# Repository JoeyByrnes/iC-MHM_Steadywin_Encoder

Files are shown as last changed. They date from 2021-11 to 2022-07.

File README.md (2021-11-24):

# iC-MHM_Steadywin_Encoder
PCB Design Files for iC-MHM Based Encoder PCB for the Steadywin v3 Motor

<p align="center">
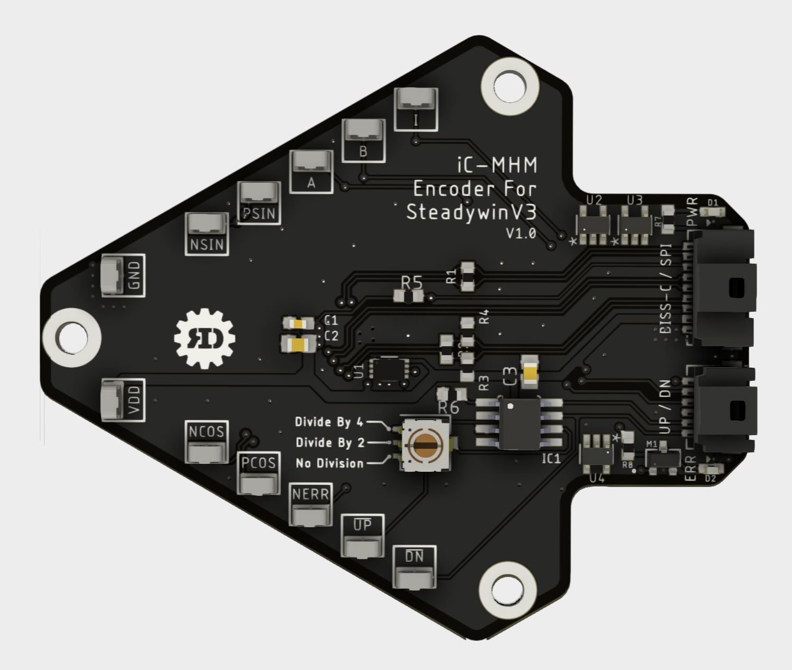
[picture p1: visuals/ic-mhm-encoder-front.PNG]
  
</p>
<p align="center">
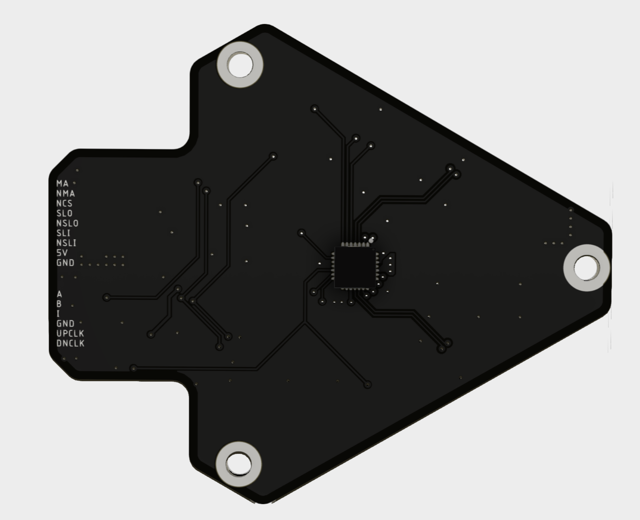
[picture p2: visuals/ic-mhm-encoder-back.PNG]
  
</p>
<p align="center">
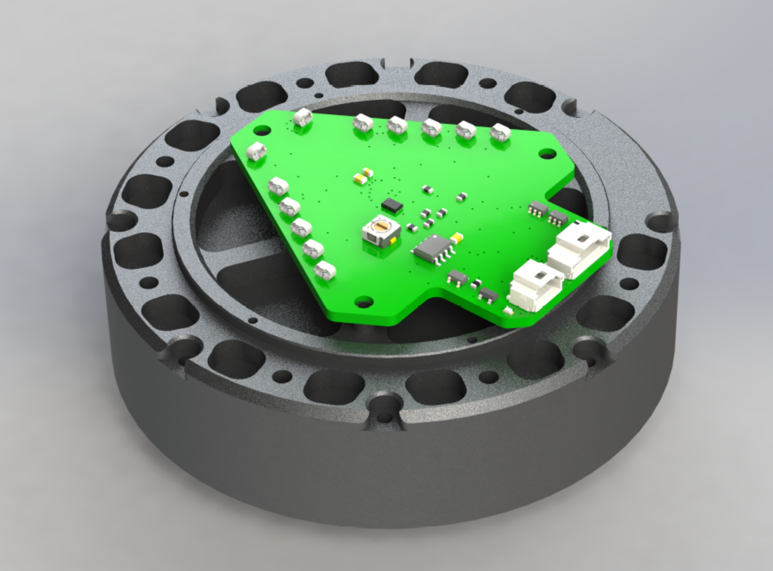
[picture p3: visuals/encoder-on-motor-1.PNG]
  
</p>

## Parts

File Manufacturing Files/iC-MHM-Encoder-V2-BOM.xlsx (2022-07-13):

Manufacturer Part Number | Manufacturer Name | Description | QTY | Digi-Key Part Number 1 | Datasheet | Reference Designator
24LC16BT-I/MC | Microchip Technology | IC EEPROM 16KBIT I2C 400KHZ 8DFN | 1 | 24LC16BT-I/MCCT-ND | https://ww1.microchip.com/downloads/en/DeviceDoc/20001703M.pdf | U1
BSS670S2LH6327XTSA1 | Infineon Technologies | MOSFET N-CH 55V 540MA SOT23-3 | 1 | BSS670S2LH6327XTSA1CT-ND | https://www.infineon.com/dgdl/BSS670S2L_Rev2.5.pdf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 | M1
D5V0F4U6S-7 | Diodes Incorporated | TVS DIODE 5.5VWM 12VC SOT363 | 4 | 31-D5V0F4U6S-7CT-ND | https://www.diodes.com/assets/Datasheets/D5V0F4U6S.pdf | U2, U3, U4, U5
06035C104K4T4A | KYOCERA AVX | CAP CER 0.1UF 50V X7R 0603 | 2 | 478-9903-1-ND | https://datasheets.kyocera-avx.com/AutoMLCC.pdf | C1, C3
0603ZD106KAT2A | KYOCERA AVX | CAP CER 10UF 10V X5R 0603 | 2 | 478-10766-1-ND | https://datasheets.kyocera-avx.com/cx5r.pdf | C2, C4
ERJ-PA3F1200V | Panasonic Electronic Components | RES SMD 120 OHM 1% 1/3W 0603 | 2 | P120BYCT-ND | https://industrial.panasonic.com/cdbs/www-data/pdf/RDO0000/AOA0000C331.pdf | R1, R2
RE0603FRE071KL | YAGEO | RES SMD 1K OHM 1% 1/10W 0603 | 2 | 13-RE0603FRE071KLCT-ND | https://www.yageo.com/upload/media/product/productsearch/datasheet/rchip/PYu-RE_105_RoHS_L_6.pdf | R7, R8
ESR03EZPF1002 | Rohm Semiconductor | RES SMD 10K OHM 1% 1/4W 0603 | 1 | RHM10KADCT-ND | https://fscdn.rohm.com/en/products/databook/datasheet/passive/resistor/chip_resistor/esr-e.pdf | R5
RC0603FR-07845RL | YAGEO | RES 845 OHM 1% 1/10W 0603 | 2 | 311-845HRCT-ND | https://www.yageo.com/upload/media/product/productsearch/datasheet/rchip/PYu-RC_Group_51_RoHS_L_11.pdf | R3, R4
150060RS75000 | Würth Elektronik | LED RED CLEAR 0603 SMD | 1 | 732-4978-1-ND | https://www.we-online.com/katalog/datasheet/150060RS75000.pdf | D2
150060VS75000 | Würth Elektronik | LED GREEN CLEAR 0603 SMD | 1 | 732-4980-1-ND | https://www.we-online.com/katalog/datasheet/150060VS75000.pdf | D1
UA9638CDR | Texas Instruments | IC DRIVER 2/0 8SOIC | 1 | 296-15058-1-ND | https://www.ti.com/general/docs/suppproductinfo.tsp?distId=10 | U6
2023960207 | Molex | CONN HEADER SMD R/A 2POS 1MM | 1 | WM26783CT-ND | https://www.molex.com/pdm_docs/sd/2023960207_sd.pdf | J1
2023961007 | Molex | CONN HEADER SMD R/A 10POS 1MM | 1 | WM26787CT-ND | https://www.molex.com/pdm_docs/sd/2023961007_sd.pdf | J2
iC-MHM | iC-Haus | https://www.ichaus.de/product/ic-mhm | 1 | N/A | https://www.ichaus.de/MHM_datasheet_en | U7

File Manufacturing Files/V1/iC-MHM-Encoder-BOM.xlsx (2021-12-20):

PCB: | Manufacturer Part Number | Manufacturer Name | Description (or link if not on digikey) | Quantity | Digi-Key Part Number 1 | Unit Price | Extended Price | Reference Designator | Datasheet
*** | 2023960607 | Molex | CONN HEADER SMD R/A 6POS 1MM | 1 | 900-2023960607CT-ND | $1.35 | $1.35 | J2 | https://www.molex.com/pdm_docs/sd/2023960607_sd.pdf
 | 2023960907 | Molex | CONN HEADER SMD R/A 9POS 1MM | 1 | WM26786CT-ND | $1.54 | $1.54 | J1 | https://www.molex.com/pdm_docs/sd/2023960907_sd.pdf
 | 24LC16BT-I/MC | Microchip Technology | IC EEPROM 16KBIT I2C 400KHZ 8DFN | 1 | 24LC16BT-I/MCCT-ND | $0.45 | $0.45 | U1 | https://ww1.microchip.com/downloads/en/DeviceDoc/20001703M.pdf
 | BSS670S2LH6327XTSA1 | Infineon Technologies | MOSFET N-CH 55V 540MA SOT23-3 | 1 | BSS670S2LH6327XTSA1CT-ND | $0.45 | $0.45 | M1 | https://www.infineon.com/dgdl/BSS670S2L_Rev2.5.pdf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
 | CS-4-13NTA | Nidec Copal Electronics | SWITCH ROTARY DIP SP3T 100MA 16V | 1 | 563-1035-1-ND | $1.81 | $1.81 | SW1 | https://www.nidec-copal-electronics.com/e/catalog/switch/cs-4.pdf
 | D5V0F4U6S-7 | Diodes Incorporated | TVS DIODE 5.5VWM 12VC SOT363 | 3 | 31-D5V0F4U6S-7CT-ND | $0.52 | $1.56 | U2, U3, U4 | https://www.diodes.com/assets/Datasheets/D5V0F4U6S.pdf
 | LS7183N-S | LSI/CSI | QUADRATURE CLOCK CONVERTER | 1 | 2808-LS7183N-S-ND | $4.89 | $4.89 | IC1 | https://lsicsi.com/datasheets/LS7183N_LS7184N.pdf
 | S1751-46 | Harwin Inc. | PC TEST POINT NATURAL | 12 | 952-3024-ND | $0.23 | $2.78 | U$2, U$3, U$4, U$5, U$6, U$7, U$8, U$9, U$10, U$11, U$15, U$16 | https://cdn.harwin.com/pdfs/S1751.pdf
 | 06035C104K4T4A | KYOCERA AVX | CAP CER 0.1UF 50V X7R 0603 | 2 | 478-9903-1-ND | $0.10 | $0.10 | C1, C4 | https://datasheets.kyocera-avx.com/AutoMLCC.pdf
 | CC0805MRX5R6BB106 | YAGEO | CAP CER 10UF 10V X5R 0805 | 2 | 311-3437-1-ND | $0.20 | $0.40 | C2, C3 | https://www.yageo.com/upload/media/product/productsearch/datasheet/mlcc/UPY-GPHC_X5R_4V-to-50V_26.pdf
 | ERJ-PA3F1200V | Panasonic Electronic Components | RES SMD 120 OHM 1% 1/4W 0603 | 2 | P120BYCT-ND | $0.15 | $0.30 | R1, R2 | https://industrial.panasonic.com/cdbs/www-data/pdf/RDO0000/AOA0000C331.pdf
 | RE0603FRE071KL | YAGEO | RES SMD 1K OHM 1% 1/10W 0603 | 5 | 13-RE0603FRE071KLCT-ND | $0.10 | $0.50 | R7, R8, R9, R10, R11 | https://www.yageo.com/upload/media/product/productsearch/datasheet/rchip/PYu-RE_105_RoHS_L_6.pdf
 | ESR03EZPF1002 | Rohm Semiconductor | RES SMD 10K OHM 1% 1/4W 0603 | 1 | RHM10KADCT-ND | $0.13 | $0.13 | R5 | https://fscdn.rohm.com/en/products/databook/datasheet/passive/resistor/chip_resistor/esr-e.pdf
 | ERJ-3EKF6493V | Panasonic Electronic Components | RES SMD 649K OHM 1% 1/10W 0603 | 1 | P649KHCT-ND | $0.10 | $0.10 | R6 | https://industrial.panasonic.com/cdbs/www-data/pdf/RDA0000/AOA0000C304.pdf
 | RC0603FR-07845RL | YAGEO | RES 845 OHM 1% 1/10W 0603 | 2 | 311-845HRCT-ND | $0.10 | $0.20 | R3, R4 | https://www.yageo.com/upload/media/product/productsearch/datasheet/rchip/PYu-RC_Group_51_RoHS_L_11.pdf
 | 150060RS75000 | Würth Elektronik | LED RED CLEAR 0603 SMD | 1 | 732-4978-1-ND | $0.15 | $0.15 | D2 | https://www.we-online.de/katalog/datasheet/150060RS75000.pdf
 | 150060VS75000 | Würth Elektronik | LED GREEN CLEAR 0603 SMD | 1 | 732-4980-1-ND | $0.15 | $0.15 | D1 | https://www.we-online.de/katalog/datasheet/150060VS75000.pdf
 | iC-MHM | iC Haus | https://www.ichaus.de/product/ic-mhm | 1 | N/A |  |  | U$1 | https://www.ichaus.de/MHM_datasheet_en
 | SN74LVC3G07QDCURQ1 | Texas Instruments | IC BUFFER NON-INVERT 5.5V 8VSSOP | 1 | 296-23710-1-ND | $0.68 | $0.68 | U5 | https://www.ti.com/general/docs/suppproductinfo.tsp?distId=10
*** | The 2023960607 is out of stock on digikey but is available on mouser: |  | https://www.mouser.com/ProductDetail/Molex/202396-0607?qs=5aG0NVq1C4ymp4Cu3BzYEA%3D%3D
Cables: |  |  |  |  |  |  |  | Notes:
 | 5011893010 | Molex | CONN RECEPT 1MM DUAL 30POS | 1 | 23-5011893010-ND | 0.68000 | $0.68 | AMC side absolute connector
 | 5013300600 | Molex | CONN RCPT 1MM VERT 6POS | 1 | WM7919-ND | 0.34000 | $0.34 | iC-MHM side incremental connector
 | 5013300900 | Molex | CONN RCPT 1MM VERT 9POS | 1 | 23-5013300900-ND | 0.41000 | $0.41 | iC-MHM side absolute connector
 | 5013340000 | Molex | CONN SOCKET 28-32AWG CRIMP TIN | 25 | WM3670CT-ND | 0.04300 | $1.08 | Crimps to make custom length cables
 | 0797581018 | Molex | PICO-CLASP 150MM 28AWG PRE-CRIMP | 20 | WM15696-ND | 1.00200 | $20.04 | One option for pre-crimped cables, only 150mm long
 |  |  |  |  |  |  |  | I order all earthsense cables from this supplier, I can check how much the cables we need would cost if we know the length needed, they're very affordable and always provide reliable cables. It usually takes about 3-4 weeks in total to receive orders
 |  |  |  |  |  |  |  | https://ykt.en.alibaba.com/?spm=a2700.12243863.0.0.38403e5f2DNDKv

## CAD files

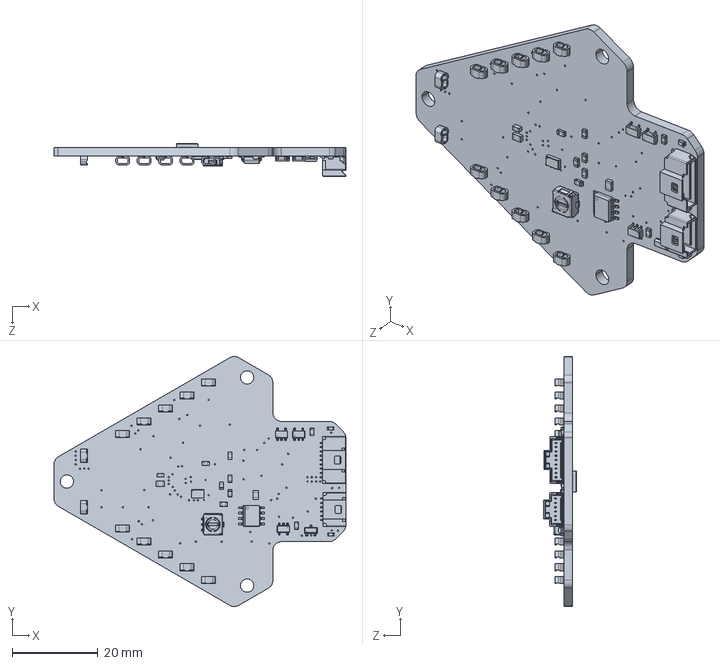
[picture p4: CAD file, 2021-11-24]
3D CAD/ic-mhm-encoder.SLDPRT
68.0 x 58.3 x 7.59 mm

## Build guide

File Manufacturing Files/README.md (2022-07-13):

# How to Order the iC-MHM Encoder:

#### The PCBs are designed to PCBWay's 4-Layer stackup, any thickness from 0.6mm to 2.4mm. 
#### If ordered elsewhere, please confirm that the layer thicknesses are correct before ordering to acheive the correct differential impedances
<hr>

## For an assembly order, enter the following:
15 Unique Components <br>
23 SMD Components total <br>
0 Thru-Hole components <br>
<p>
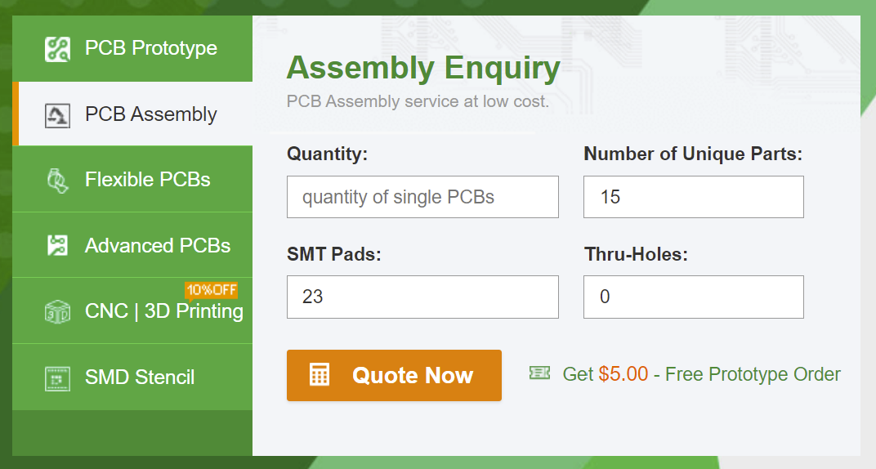
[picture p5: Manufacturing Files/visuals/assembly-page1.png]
  
</p>

### See readme in V1 folder for PCB options, but remember the following changes:
#### The size of the PCB is now 63mm x 58mm (not 68x58)
#### The thickness can be anything from 0.6mm to 2.4mm now
#### the stencil doesnt apply for an assembly order
#### Make sure to upload both the BOM and the zip file which contains the gerbers and the PnP files

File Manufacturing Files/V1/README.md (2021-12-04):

# How to Order the iC-MHM Encoder:

<b>
The PCBs are designed to PCBWay's 4-Layer 2mm stackup. If ordered elsewhere, please confirm that the layer thicknesses are correct before ordering to acheive the correct differential impedances.
</b>
<h2>On the first page of PCBway, enter the following:
<p align="center">
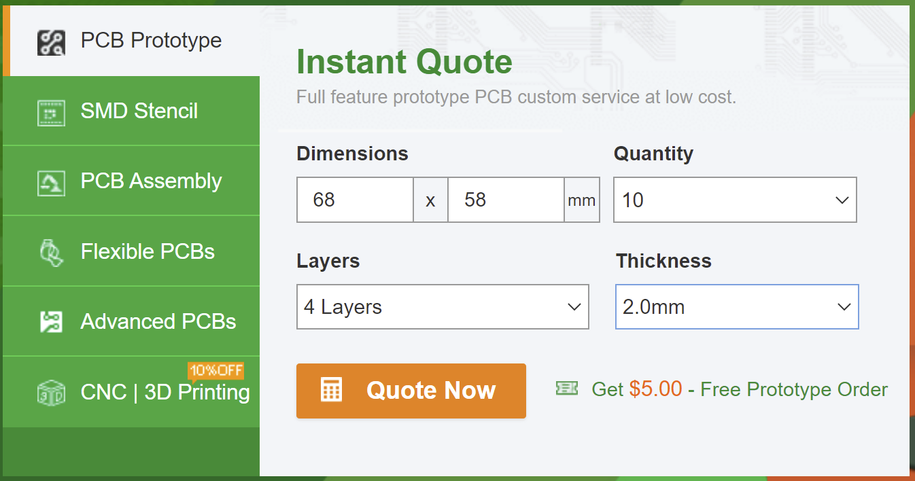
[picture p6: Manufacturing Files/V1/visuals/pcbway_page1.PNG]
  
</p>

On the ordering page, make sure to select 2mm, and choose the color black if you don't want a lame green pcb
<p align="center">
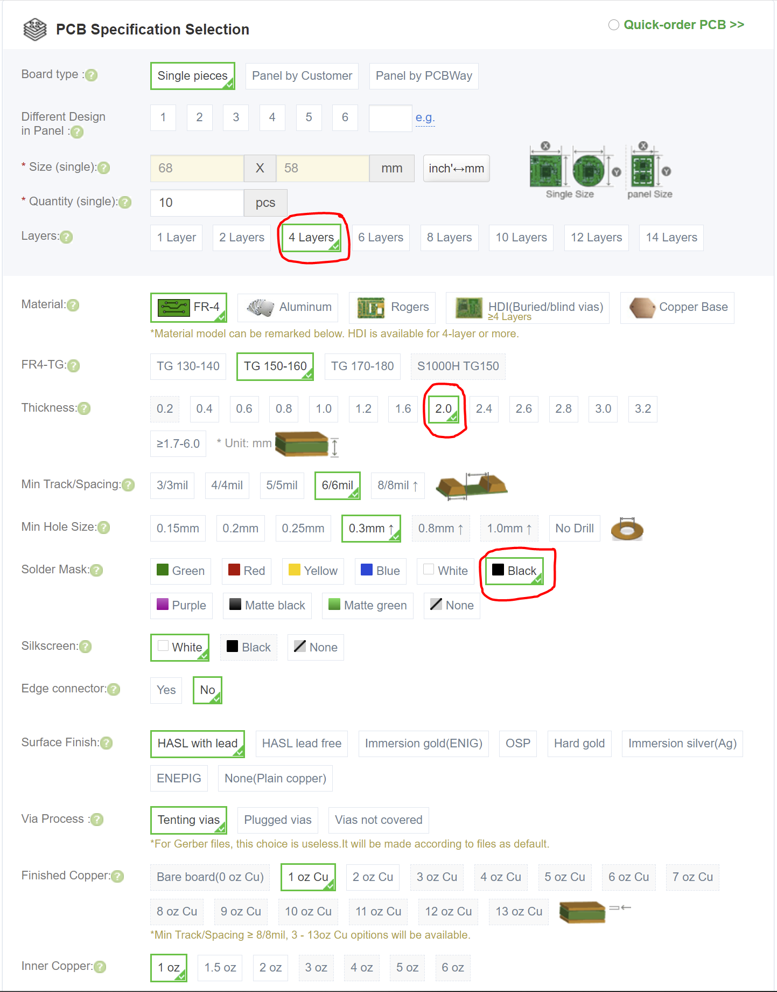
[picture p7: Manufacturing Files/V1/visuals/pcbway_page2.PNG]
  
</p>

Make sure to order a stencil, and that you select Top+Bottom. I find that without framework is easier to use.
<p align="center">
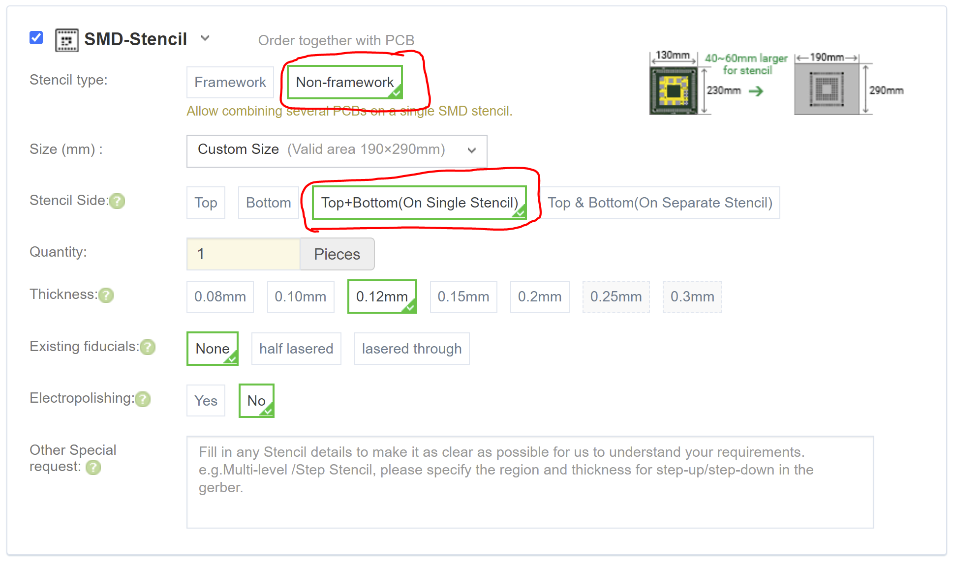
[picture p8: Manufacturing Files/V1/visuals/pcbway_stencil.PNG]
  
</p>

This should be the approximate cost if entered correctly, based on data from 12/4/21
<p align="center">
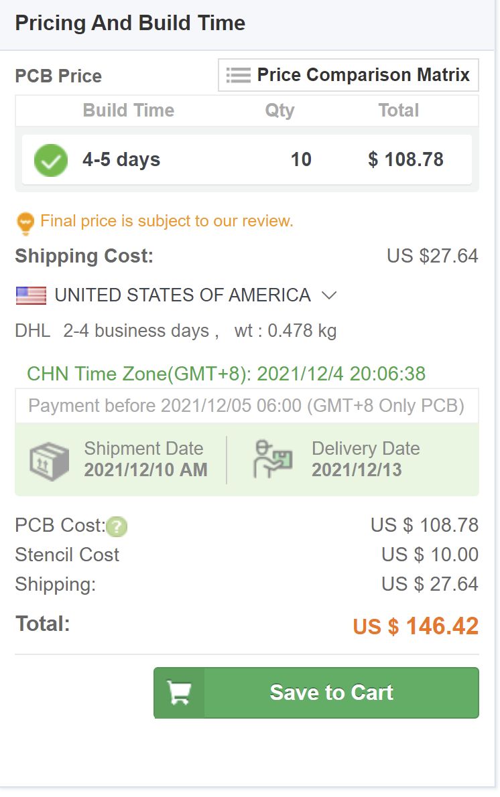
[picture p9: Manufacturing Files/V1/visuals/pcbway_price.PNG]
  </h2>
</p>

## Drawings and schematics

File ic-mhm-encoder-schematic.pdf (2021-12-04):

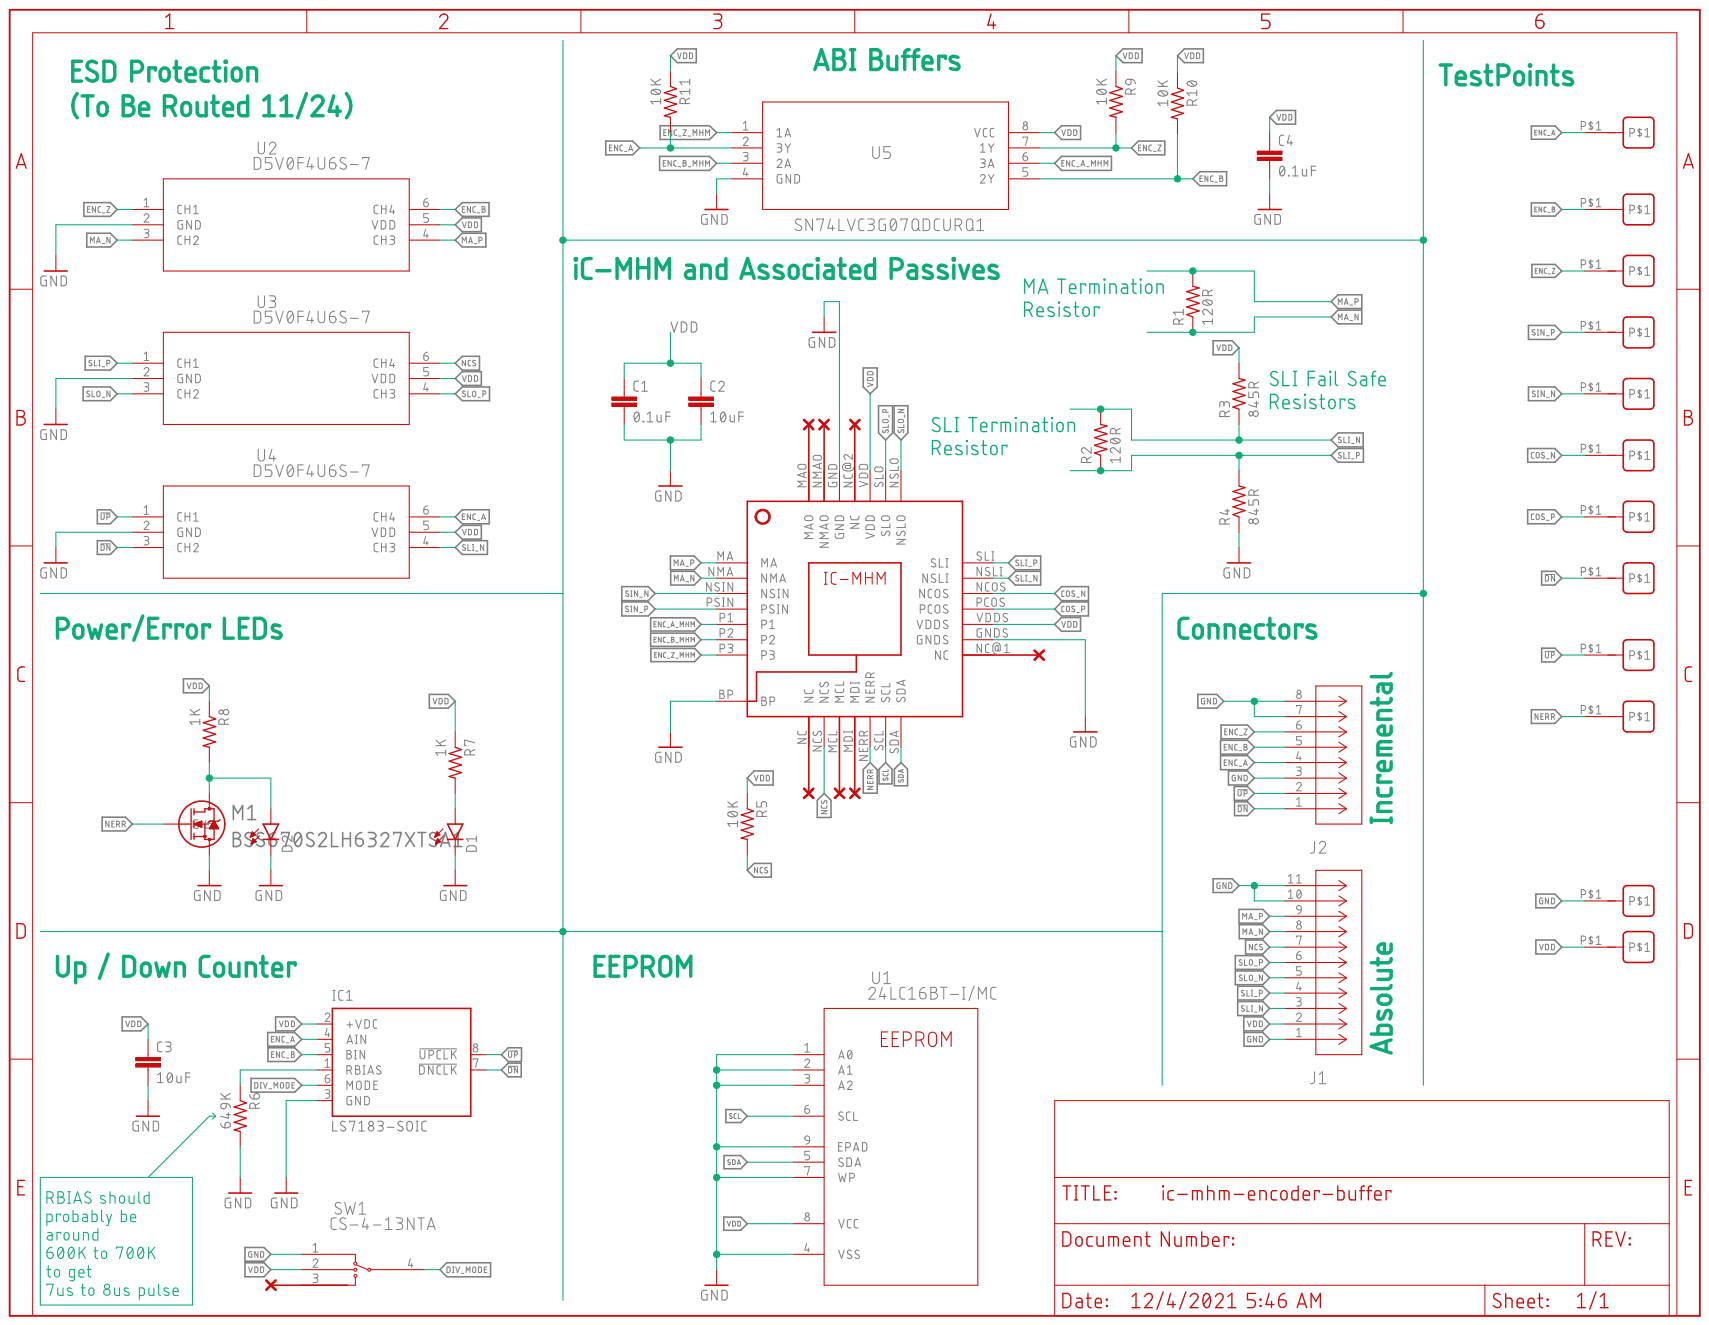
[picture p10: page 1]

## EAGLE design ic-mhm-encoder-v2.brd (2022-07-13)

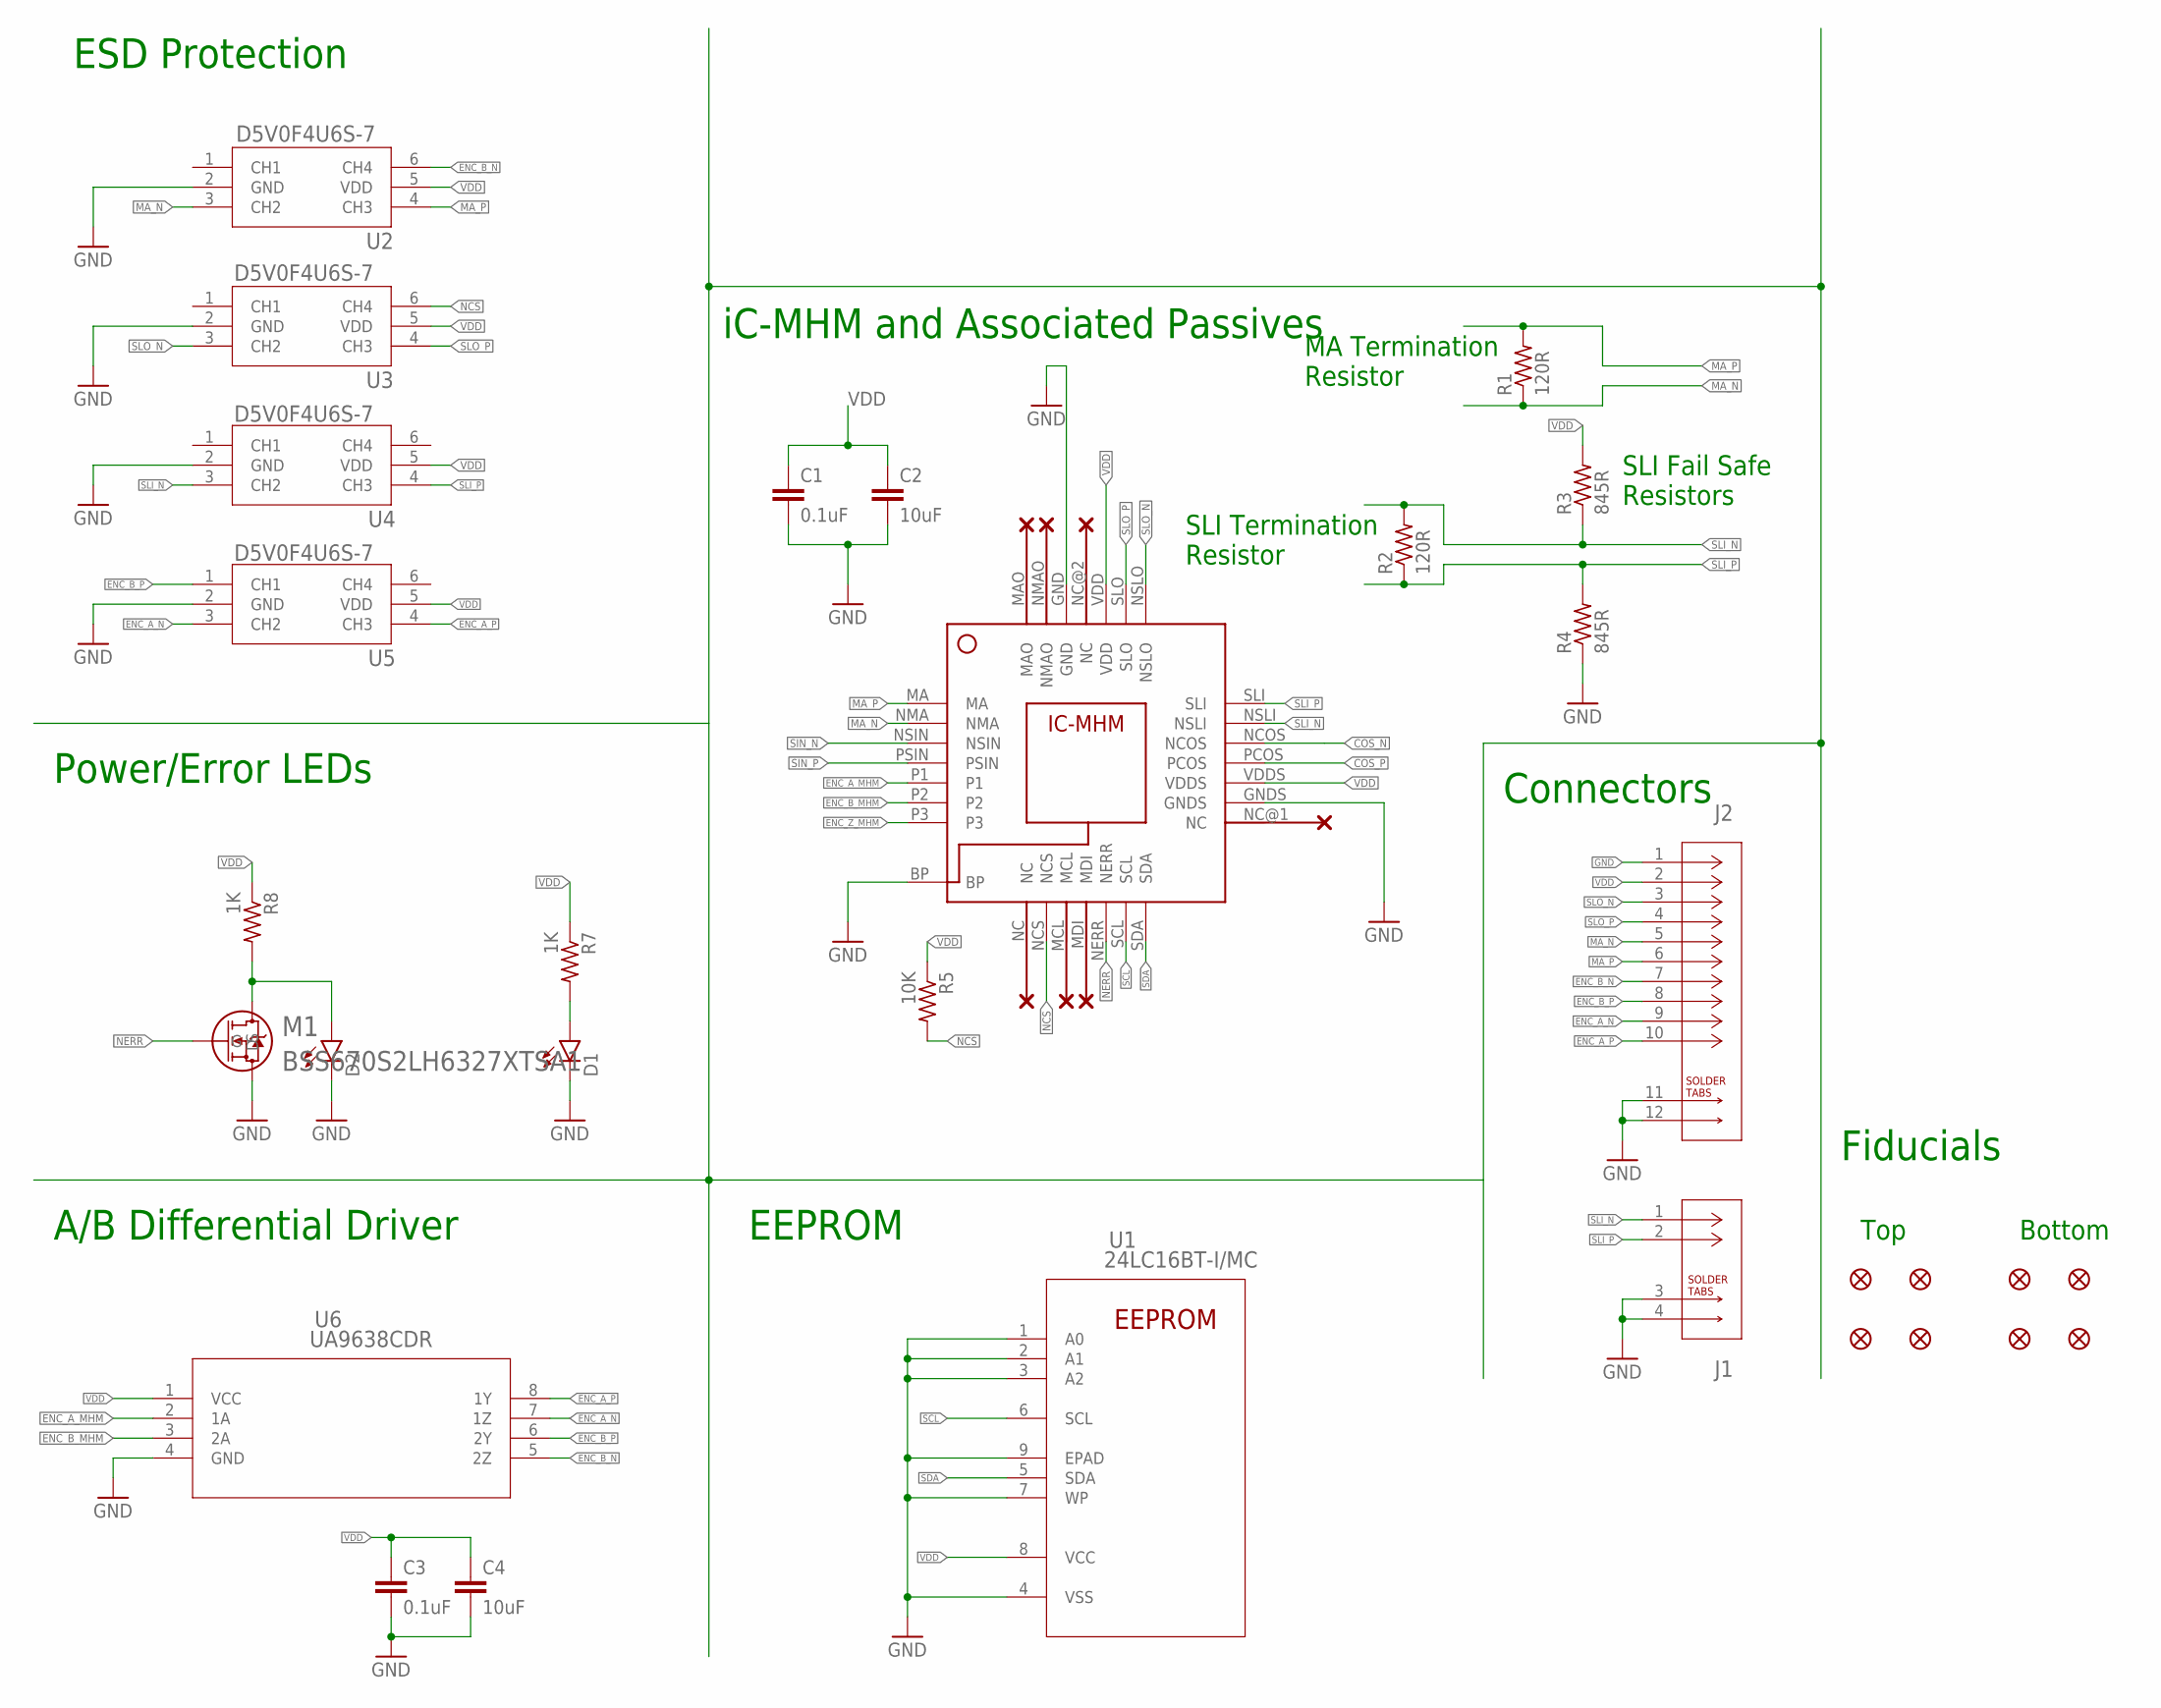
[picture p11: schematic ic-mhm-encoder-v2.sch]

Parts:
C1, C3: 0.1uF; C0603
C2, C4: 10uF; C0603
D1, D2: LEDSML0603; SML0603
FID1, FID2, FID3, FID4, FID5, FID6, FID7, FID8: FIDUCIAL_1MM
J1: 2023960207; CON_2023960207
J2: 2023961007; CON_2023961007
M1: BSS670S2LH6327XTSA1; PG-SOT23-3-5_INF
R1, R2: 120R; R0603
R3, R4: 845R; R0603
R5: 10K; R0603
R7, R8: 1K; R0603
U1: 24LC16BT-I/MC; DFN8_2X3MC_MCH
U2, U3, U4, U5: D5V0F4U6S-7; SOT-363_DIO
U6: UA9638CDR; D8
U$1: IC-MHM

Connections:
COS_N: U$1.NCOS
COS_P: U$1.PCOS
ENC_A_MHM: U6.2 (1A), U$1.P1
ENC_A_N: J2.9, U5.3 (CH2), U6.7 (1Z)
ENC_A_P: J2.10, U5.4 (CH3), U6.8 (1Y)
ENC_B_MHM: U6.3 (2A), U$1.P2
ENC_B_N: J2.7, U2.6 (CH4), U6.5 (2Z)
ENC_B_P: J2.8, U5.1 (CH1), U6.6 (2Y)
ENC_Z_MHM: U$1.P3
GND: C1.2, C2.2, C3.2, C4.2, D1.C, D2.C, J1.3, J1.4, J2.1, J2.11, J2.12, M1.2 (S), R4.1, U1.1 (A0), U1.2 (A1), U1.3 (A2), U1.4 (VSS), U1.7 (WP), U1.9 (EPAD), U2.2 (GND), U3.2 (GND), U4.2 (GND), U5.2 (GND), U6.4 (GND), U$1.BP, U$1.GND, U$1.GNDS
MA_N: J2.5, R1.1, U2.3 (CH2), U$1.NMA
MA_P: J2.6, R1.2, U2.4 (CH3), U$1.MA
unnamed: D1.A, R7.2
unnamed: D2.A, M1.3 (D), R8.2
NCS: R5.2, U3.6 (CH4), U$1.NCS
NERR: M1.1 (G), U$1.NERR
SCL: U1.6 (SCL), U$1.SCL
SDA: U1.5 (SDA), U$1.SDA
SIN_N: U$1.NSIN
SIN_P: U$1.PSIN
SLI_N: J1.1, R2.2, R3.1, U4.3 (CH2), U$1.NSLI
SLI_P: J1.2, R2.1, R4.2, U4.4 (CH3), U$1.SLI
SLO_N: J2.3, U3.3 (CH2), U$1.NSLO
SLO_P: J2.4, U3.4 (CH3), U$1.SLO
VDD: C1.1, C2.1, C3.1, C4.1, J2.2, R3.2, R5.1, R7.1, R8.1, U1.8 (VCC), U2.5 (VDD), U3.5 (VDD), U4.5 (VDD), U5.5 (VDD), U6.1 (VCC), U$1.VDD, U$1.VDDS

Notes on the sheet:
MA Termination Resistor
SLI Termination Resistor
SLI Fail Safe Resistors
ESD Protection
iC-MHM and Associated Passives
Fiducials
Power/Error LEDs
A/B Differential Driver
EEPROM
Connectors
Top
Bottom

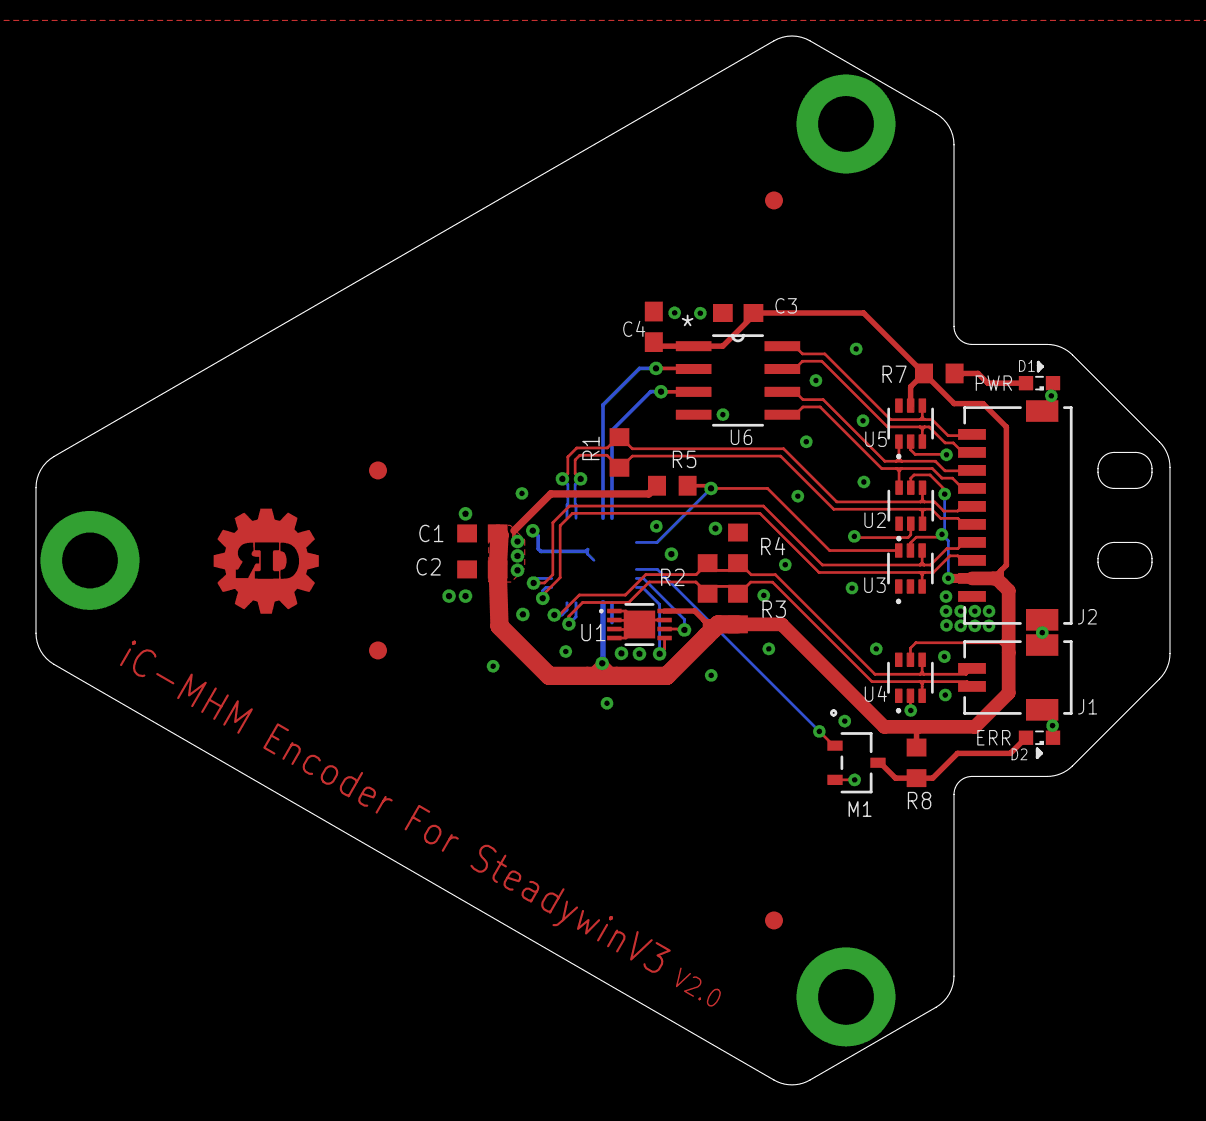
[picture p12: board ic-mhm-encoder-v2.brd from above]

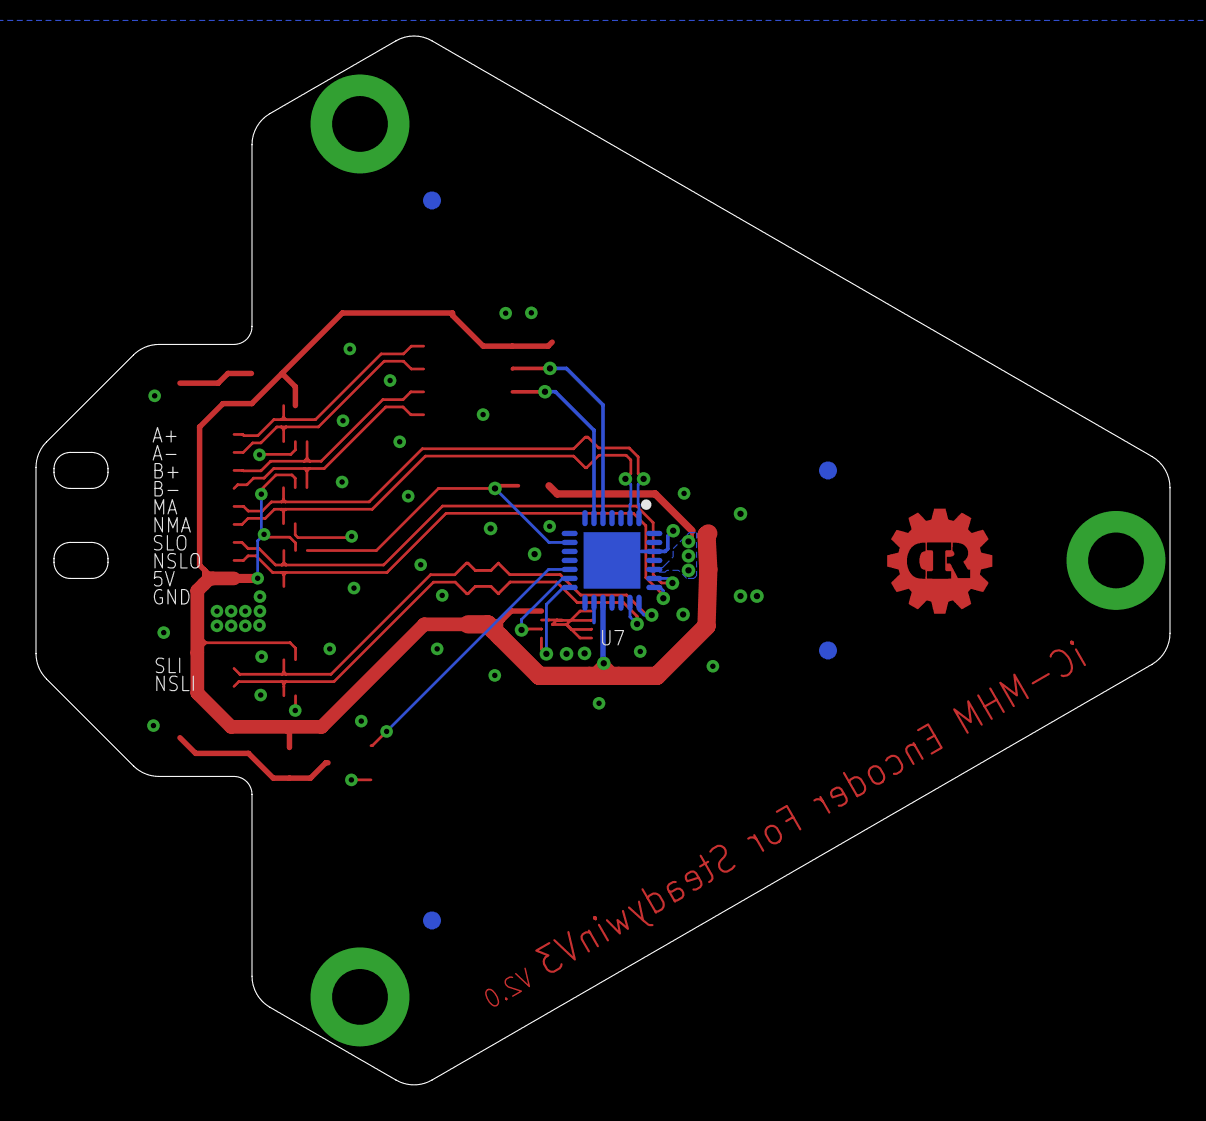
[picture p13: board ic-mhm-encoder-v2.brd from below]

Board: 4 copper layers, 63.0 x 58.3 mm, 31 parts (5 on the bottom side), 20 nets.

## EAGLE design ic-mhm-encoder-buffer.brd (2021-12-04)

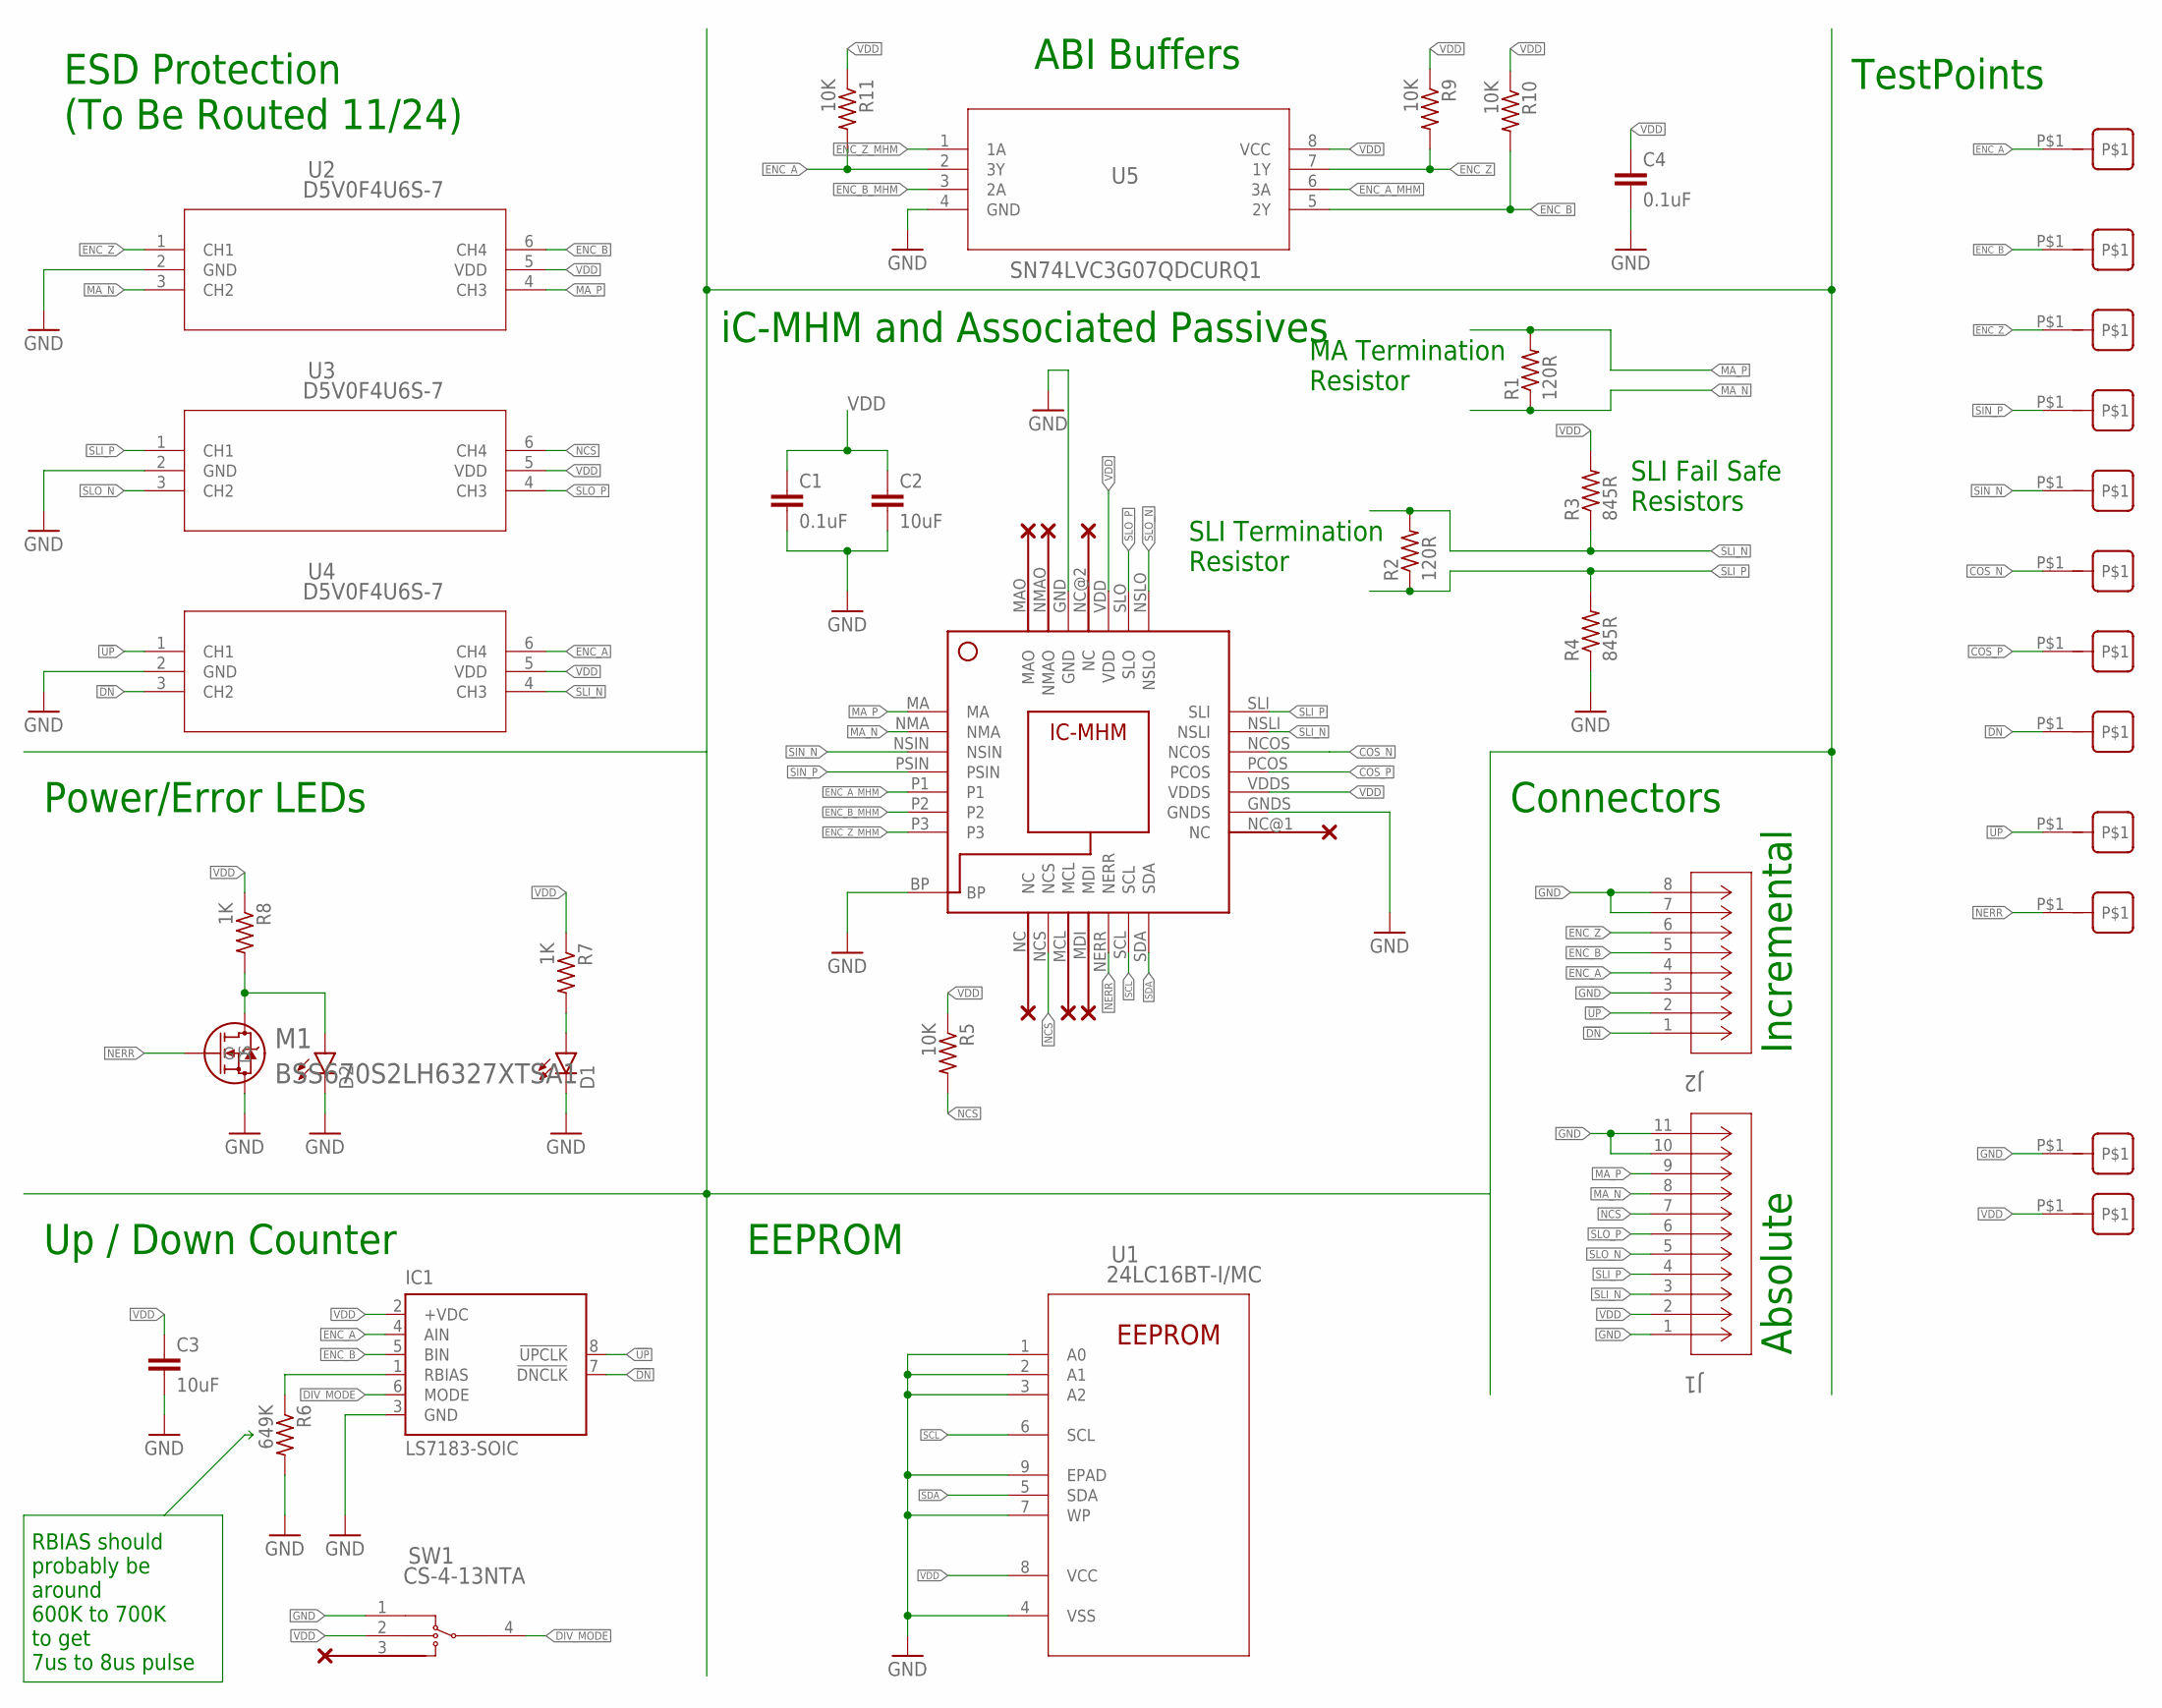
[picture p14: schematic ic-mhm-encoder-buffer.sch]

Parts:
C1, C4: 0.1uF; C0603
C2, C3: 10uF; C0805
D1, D2: LEDSML0603; SML0603
IC1: LS7183-SOIC; SOIC08
J1: 2023960907; CON_2023960907
J2: 2023960607; CON_2023960607
M1: BSS670S2LH6327XTSA1; PG-SOT23-3-5_INF
R1, R2: 120R; R0603
R3, R4: 845R; R0603
R5, R9, R10, R11: 10K; R0603
R6: 649K; R0603
R7, R8: 1K; R0603
SW1: CS-4-13NTA; CS-4-13NA_NDC
U1: 24LC16BT-I/MC; DFN8_2X3MC_MCH
U2, U3, U4: D5V0F4U6S-7; SOT-363_DIO
U5: SN74LVC3G07QDCURQ1; DCU8_TEX
U$1: IC-MHM
U$2, U$3, U$4, U$5, U$6, U$7, U$8, U$9, U$10, U$11, U$15, U$16: TESTPOINT_S1751-46

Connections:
!DN: IC1.7 (!DNCLK), J2.1, U4.3 (CH2), U$8.P$1
!UP: IC1.8 (!UPCLK), J2.2, U4.1 (CH1), U$9.P$1
COS_N: U$1.NCOS, U$7.P$1
COS_P: U$1.PCOS, U$11.P$1
DIV_MODE: IC1.6 (MODE), SW1.4
ENC_A: IC1.4 (AIN), J2.4, R11.2, U4.6 (CH4), U5.2 (3Y), U$2.P$1
ENC_A_MHM: U5.6 (3A), U$1.P1
ENC_B: IC1.5 (BIN), J2.5, R10.2, U2.6 (CH4), U5.5 (2Y), U$3.P$1
ENC_B_MHM: U5.3 (2A), U$1.P2
ENC_Z: J2.6, R9.2, U2.1 (CH1), U5.7 (1Y), U$4.P$1
ENC_Z_MHM: U5.1 (1A), U$1.P3
GND: C1.2, C2.2, C3.2, C4.2, D1.C, D2.C, IC1.3 (GND), J1.1, J1.10, J1.11, J2.3, J2.7, J2.8, M1.2 (S), R4.1, R6.2, SW1.1, U1.1 (A0), U1.2 (A1), U1.3 (A2), U1.4 (VSS), U1.7 (WP), U1.9 (EPAD), U2.2 (GND), U3.2 (GND), U4.2 (GND), U5.4 (GND), U$1.BP, U$1.GND, U$1.GNDS, U$15.P$1
MA_N: J1.8, R1.1, U2.3 (CH2), U$1.NMA
MA_P: J1.9, R1.2, U2.4 (CH3), U$1.MA
unnamed: IC1.1 (RBIAS), R6.1
unnamed: D1.A, R7.2
unnamed: D2.A, M1.3 (D), R8.2
NCS: J1.7, R5.2, U3.6 (CH4), U$1.NCS
NERR: M1.1 (G), U$1.NERR, U$10.P$1
SCL: U1.6 (SCL), U$1.SCL
SDA: U1.5 (SDA), U$1.SDA
SIN_N: U$1.NSIN, U$6.P$1
SIN_P: U$1.PSIN, U$5.P$1
SLI_N: J1.3, R2.2, R3.1, U4.4 (CH3), U$1.NSLI
SLI_P: J1.4, R2.1, R4.2, U3.1 (CH1), U$1.SLI
SLO_N: J1.5, U3.3 (CH2), U$1.NSLO
SLO_P: J1.6, U3.4 (CH3), U$1.SLO
VDD: C1.1, C2.1, C3.1, C4.1, IC1.2 (+VDC), J1.2, R3.2, R5.1, R7.1, R8.1, R9.1, R10.1, R11.1, SW1.2, U1.8 (VCC), U2.5 (VDD), U3.5 (VDD), U4.5 (VDD), U5.8 (VCC), U$1.VDD, U$1.VDDS, U$16.P$1

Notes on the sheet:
MA Termination Resistor
SLI Termination Resistor
SLI Fail Safe Resistors
ESD Protection (To Be Routed 11/24)
iC-MHM and Associated Passives
TestPoints
Power/Error LEDs
Up / Down Counter
EEPROM
Connectors
Absolute
Incremental
RBIAS should probably be around 600K to 700K to get 7us to 8us pulse
ABI Buffers

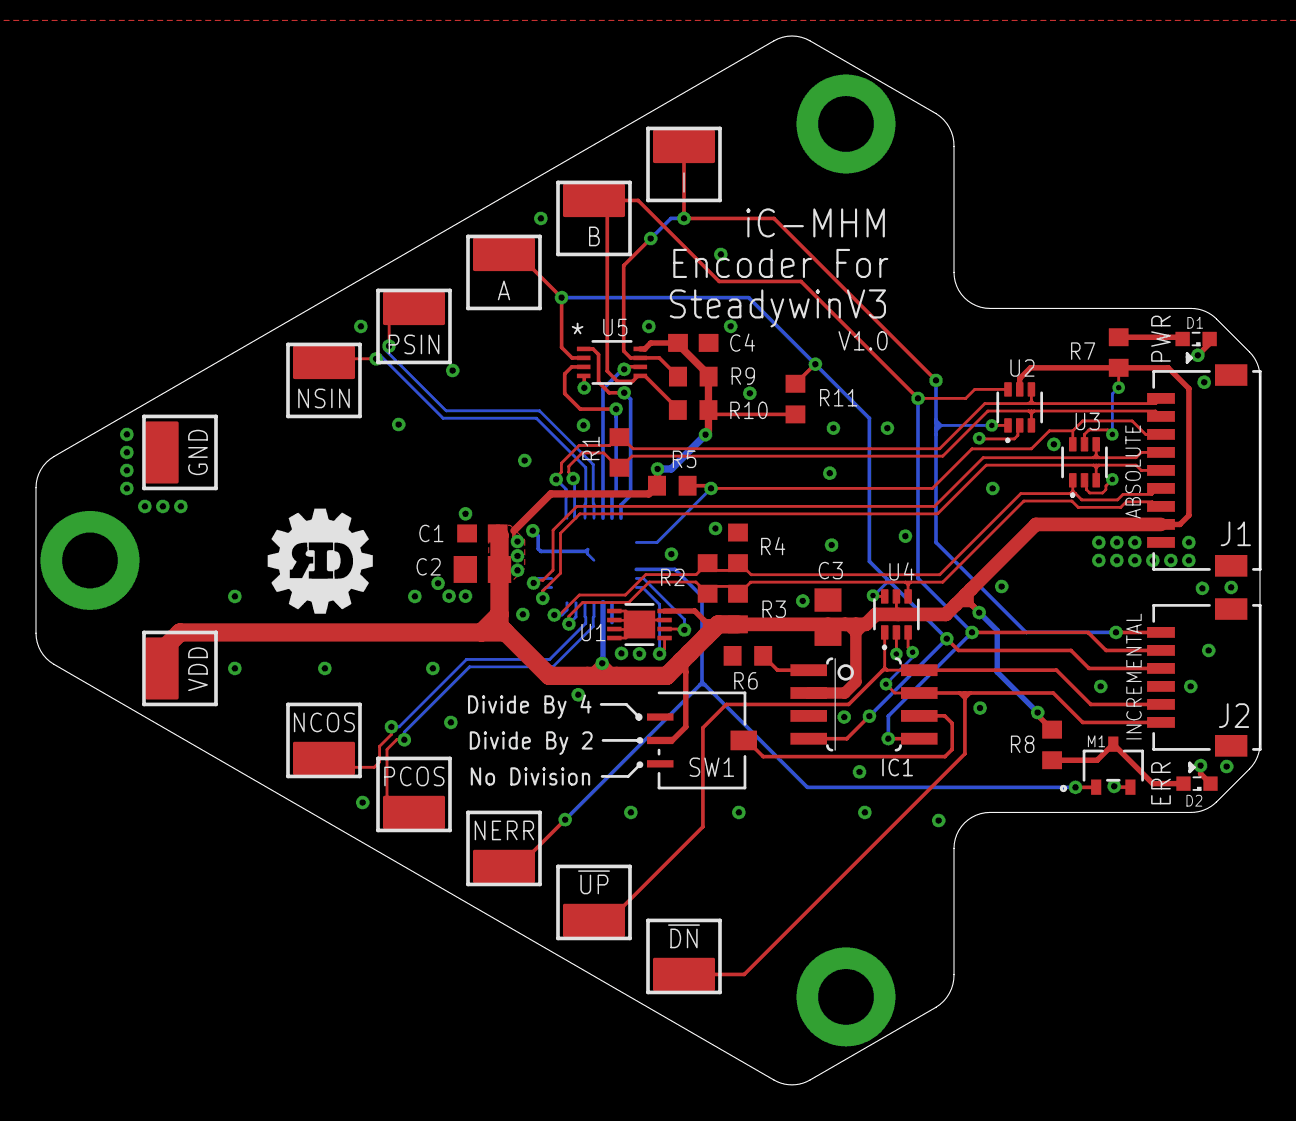
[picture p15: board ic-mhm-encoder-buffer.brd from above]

Board: 4 copper layers, 68.0 x 58.3 mm, 40 parts (1 on the bottom side), 28 nets.

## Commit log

2021-11-24 Layout almost complete, ESD diodes needs routing, Review needed
    [ic-mhm-encoder-simple.brd, ic-mhm-encoder-simple.sch]
2021-11-24 added 3D model of Encoder
    [ic-mhm-encoder.SLDPRT]
2021-11-29 Routed ESD Diodes
    [ic-mhm-encoder-simple.brd, ic-mhm-encoder-simple.sch]
2021-11-29 changed RBIAS and added note about range
    [ic-mhm-encoder-simple.brd, ic-mhm-encoder-simple.sch]
2021-12-01 Added Bill of Materials
    [iC-MHM-Encoder-BOM.xlsx]
2021-12-01 Added PDF Schematic
2021-12-01 Improved GND vias
    [ic-mhm-encoder-simple.brd]
2021-12-01 Fixed/Approved all DRC Errors
    [ic-mhm-encoder-simple.brd]
2021-12-01 moved termination resistors closer to mhm
    [ic-mhm-encoder-simple.brd]
2021-12-04 added verisons with buffers on ABI
    [ic-mhm-encoder-buffer-output-only.brd, ic-mhm-encoder-buffer-output-only.sch, ic-mhm-encoder-buffer.brd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]
2021-12-04 Updated BOM with buffer components
    [iC-MHM-Encoder-BOM.xlsx]
2021-12-04 moved unused designs to alternate designs folder
    [ic-mhm-encoder-buffer-output-only.brd, ic-mhm-encoder-buffer-output-only.sch, ic-mhm-encoder-simple.brd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]
2021-12-04 updated pdf to schematic with buffers
2021-12-04 Added GERBERs with how to order ReadME
2021-12-04 Design Ready to Order
    [ic-mhm-encoder-buffer.brd]
2021-12-20 switched to 1k pullups and 0805 10uF
    [iC-MHM-Encoder-BOM.xlsx]
2022-03-25 Added config file for working BISS-C configuration
    [working-mhm.cfg]
2022-06-28 V2 encoder work in progress
    [ic-mhm-encoder-v2.brd, ic-mhm-encoder-v2.sch]
2022-07-07 Finished routing of v2 pcb, ready for design review
    [ic-mhm-encoder-v2.brd, ic-mhm-encoder-v2.sch]
2022-07-08 added zip tie slots
    [ic-mhm-encoder-v2.brd]
2022-07-13 added mfg and assembly files for v2
    [iC-MHM-Encoder-BOM.xlsx, iC-MHM-Encoder-V2-BOM.xlsx, ic-mhm-encoder-v2.brd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]
2022-07-13 V2 PCB Ready for Assembly Order
    [ic-mhm-encoder-v2.brd]

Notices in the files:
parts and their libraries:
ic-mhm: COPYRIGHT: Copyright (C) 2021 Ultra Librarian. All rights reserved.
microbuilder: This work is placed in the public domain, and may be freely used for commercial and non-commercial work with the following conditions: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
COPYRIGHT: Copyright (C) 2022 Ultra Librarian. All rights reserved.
